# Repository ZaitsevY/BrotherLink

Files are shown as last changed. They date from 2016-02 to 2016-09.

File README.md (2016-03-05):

# Wireless Brother KH-9xx knitting machine connection.

Isn't your Brother KH-9xx online and blogging yet :smile:?<br>
Come on, stop wiring your room, it's time for **IoT** and **WiFi**!<br>
Let's create **wireless** BrotherLink cable!

## TL;DR
[Watch it working](#video)

## Briefly
- Assemble [Hardware](#hardware)
- Upload [Firmware](#firmware)
- Knit with [DesignaKnit](#software-windows-only)

## Introduction

You all know that BrotherLink BLx USB cables are far overpriced. Some of you create 
DIY cables following [Adafruit](https://learn.adafruit.com/electroknit?view=all)
or [Daviworks](http://daviworks.com/knitting/cable_tutorial.html) tutorials.
Having repeated their cable I got an idea to replace the wired connection
with a WiFi one.

After looking around I found that there's a pretty cheap solution out there on
the market – ESP8266 module, which is actually an MCU (micro controller unit)
with built-in SPI flash memory, WiFi, GPIO, UART, etc. periphery. It is very
popular for DIY IoT projects, has a lot of users, who contributed a lot of
libraries helping to develop ESP8266 applications using pure C/C++, Arduino
Wiring, Lua and so on.

## Hardware

I'm not an electronic engineer so I decided to go with ready-to-use modules 
to reduce welding and avoid mistakes. As for the minimum you need:

1. ESP8266 module (or board). I selected [WeMos D1 mini](http://www.wemos.cc/wiki/doku.php?id=en:d1_mini) -
a minimalist ESP8266 board with all necessary resistors, an integrated USB-UART 
bridge (you won't need a separate converter to connect the module to PC for firmware
flashing) and a 5V-to-3.3V power converter (not very reliable though).
2. Logic level converter. Brother KH-9xx serial interface is known to operate at 5V level,
while ESP8266 IO expects 3.3V. The simplest logic level conversion can be achieved with
two resistors by I opted to use a factory manufactured module. I bought mine from
[AliExpress](http://www.aliexpress.com/item/5pcs-lot-4-channel-IIC-I2C-Logic-Level-Converter-Bi-Directional-Module-5V-to-3-3V/32308637756.html)
which is times cheaper than the one from [SparkFun](https://www.sparkfun.com/products/12009).
*Caution*: do not! connect ESP8266 RX/TX directly to KH-9xxx port, doing so will 
most likely harm the module.
3. Power. ESP8266 operates at 3.3V (caution!); to coordinate logic levels you'll
also need 5V. For the time writing the article I feed my device with a breadboard
power supply (note separate +5V and +3.3V buses on the diagram), but for a final
setup I'm going to pick up +5V directly from KH-9xx internals in order to get rid
of wires completely. To step +5V down to +3.3V you should consider including a
separate [AMS1117 power module](http://www.aliexpress.com/item/Free-shipping-5pcs-lot-AMS1117-3-3V-power-supply-module-AMS1117-3-3-power-module-AMS1117/1996263198.html)
(not shown on the diagram). 
4. Optionally, to provide for Interactive Knitting (IK)  mode of the [DesignaKnit](https://www.softbyte.co.uk/designaknit.htm)
application, you might want to add a reed switch and a 10kOm resistor (or, like
did I, use a pre-manufactured [reed switch module](http://www.aliexpress.com/item/Free-Shipping-Reed-sensor-module-magnetron-module-reed-switch-magnetic-switch-for-arduino/1946556259.html)).
You also need a magnet, which you'll put (glue or somehow attach) to the carriage
of the knitting machine (that'll be your BL5 “magnetic arm”). With this option
your device becomes a BrotherLink BL5 wireless cable, while without it – just BL1.

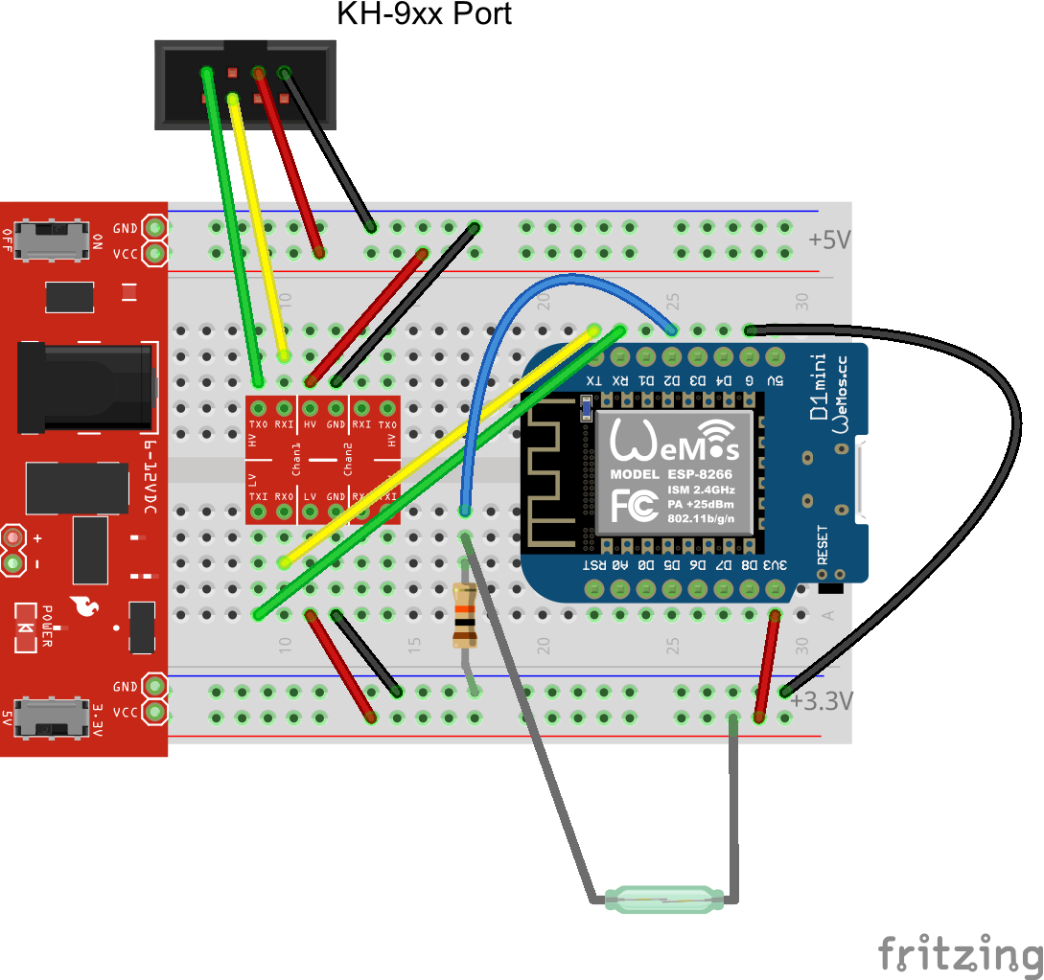
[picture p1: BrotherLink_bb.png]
Diagram


## Firmware

To make things fly you'll have to upload some firmware to the ESP8266.

The best option for those who are not close to MCU firmware programing
is to download ready-to-flash binary files from the [release](../../releases/).

The firmware is based on [esp8266web](https://github.com/pvvx/esp8266web) 
project which already contains almost all the necessary things including: 
WEB Server, TCP-to-UART bridge with a lot of configurable options, device 
and application configuration through web interface.

I had to make some customizations of the original project in order to 
utilize reed switch and provide for Interactive Knitting. Customized 
sources are [here](https://github.com/ZaitsevY/esp8266web/tree/custom) 
and the sources of the application (Eclipse project) are right in this
very repository.
Again, to skip the time consuming learning trail of compiling firmware 
from sources, you might prefer to download the [ready-to-flash binary files](../../releases/).

To upload firmware to your module you'll have to install [Python](https://www.python.org/downloads/) 
(choose 2.x version) with [pyserial](https://pythonhosted.org/pyserial/) 
(the simplest way is to issue `pip install pyserial` from command prompt 
after Python installation). [Esptool](https://github.com/themadinventor/esptool) 
is already included in the binary distribution. If you follow me and use 
WeMos D1 mini module, make sure you have installed [Ch340G driver](http://www.wemos.cc/wiki/doku.php?id=en:ch340g) 
(if appropriate for your OS). 

Connect your module to USB of your PC, detect the resulting COM-port number.<br>
*Note:* COM4 is assumed for the example commands below.<br>
*Note:* click RESET button of D1 mini just before you run `esptool.py … write_flash …` command.

First, flash clear settings with the following from the command prompt:
```
esptool.py --port COM4 --baud 460800 write_flash -ff 80m -fm qio -fs 4m 0x79000 clear_eep.bin 0x7C000 esp_init_data_default.bin 0x7E000 blank.bin
```

Second, flash the software portion:
```
esptool.py --port COM4 --baud 460800 write_flash -ff 80m -fm qio -fs 4m 0x00000 .0x00000.bin 0x07000 .0x07000.bin
```

Press RESET on the module again (just to be on the safe side), wait a
couple of seconds and now you can use any of your WiFi-enabled 
devices (notebook, smartphone) to:

1. Connect to a WiFi access point named ESP8266 (by default);
2. Point you browser to http://192.168.4.1/fsupload (default username:password 
are ESP8266:0123456789) and upload WEBFiles.bin file;
3. Point you browser to http://192.168.4.1/ and continue device configuration.

### Configuration:

1. WiFi Settings: set your home WiFi SSID and password. Optionally switch off 
ESP8266 access point by selecting STATION_MODE. Mention that right after switching 
AP off you won't be able to access web interface of the module with 192.168.4.1, 
instead reconnect your notebook (or whatever) back to your home network and 
use [http://sesp8266/](http://sesp8266/) or, if the latter doesn't work for you,
find out the new module IP address from your WiFi router (notice http://192.168.1.37/ 
address part on the screenshots below). Or just leave WiFi mode setting as STATIONAP_MODE.<br>
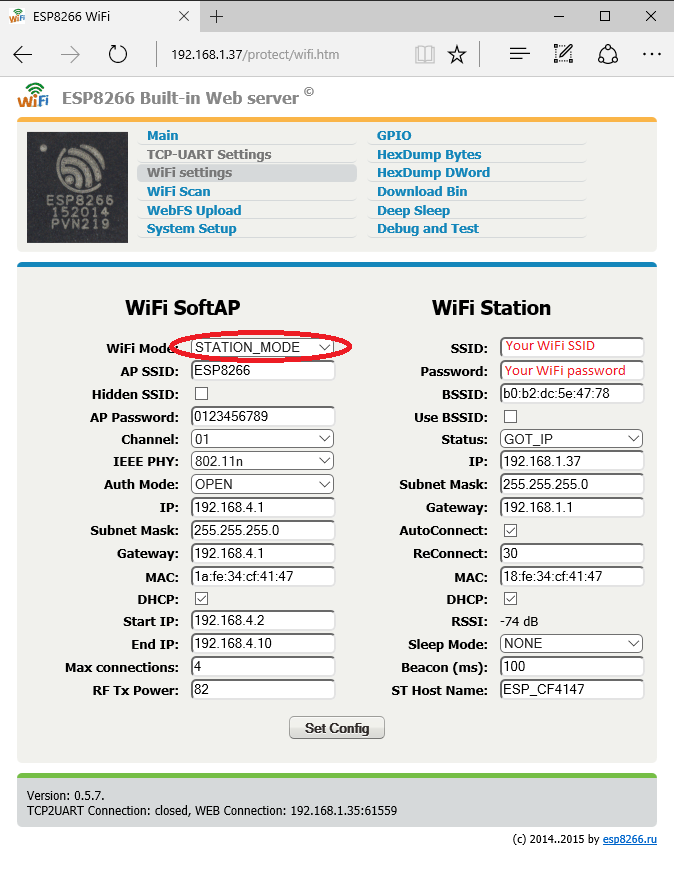
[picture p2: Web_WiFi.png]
WiFi Settings

2. TCP-TO-UART Settings: set baud rate to 9600, enable RX and TX inversion.<br>
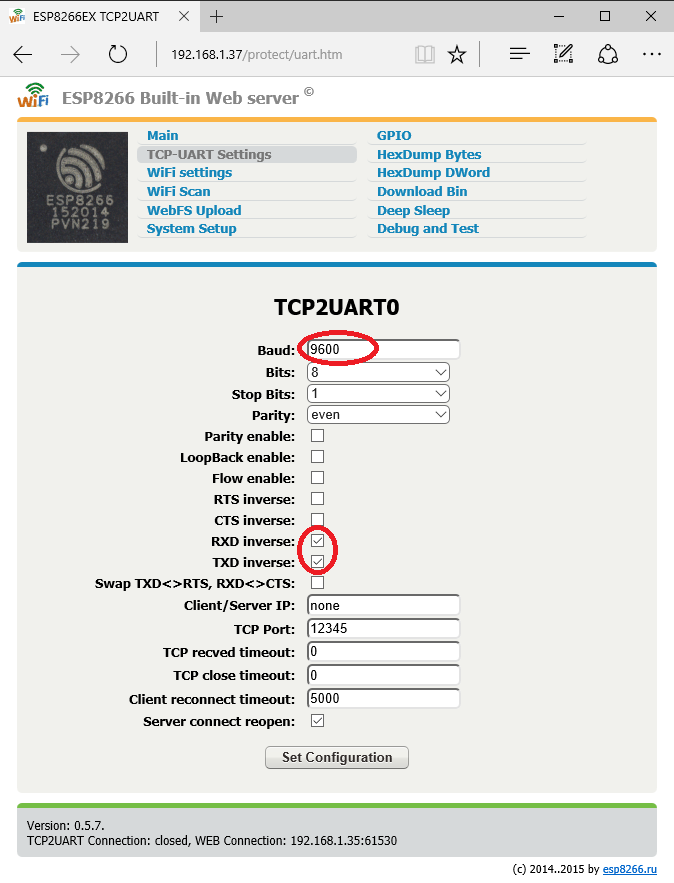
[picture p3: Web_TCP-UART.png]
TCP=UART Settings

3. System Setup: disable checking RX pin to reset WiFi configuration (*important!* 
When you power on your device while it is connected to KH-9xx port, this setting, 
if enabled, will reset your customizations from 1.).<br>
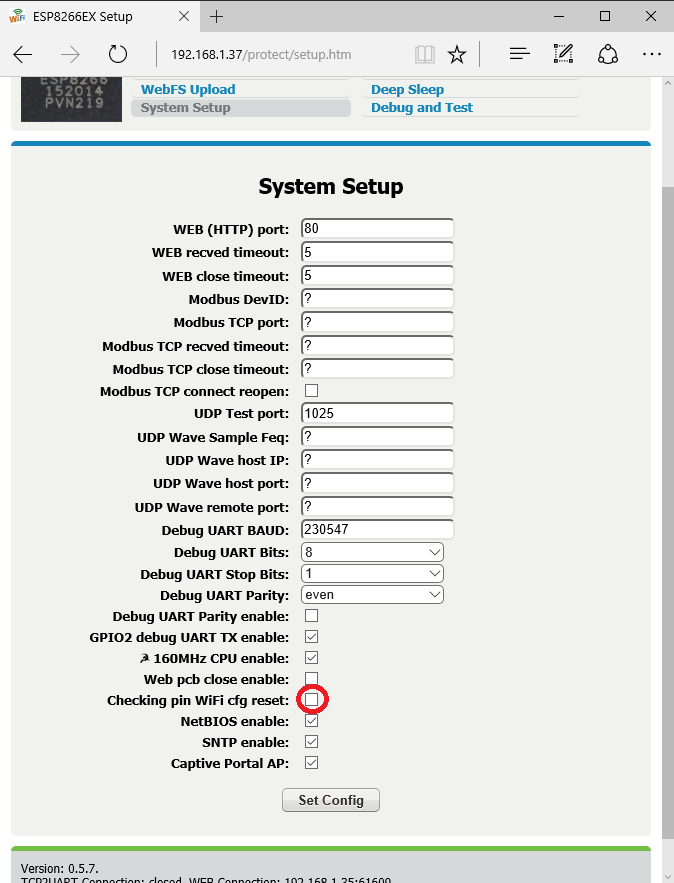
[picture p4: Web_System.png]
System Settings


## Software (Windows only)

DesignaKnit expects knitting machine to be connected through COM interface. 
To make it acquainted with your device you'd install a virtual COM-port driver. 
There are several solutions out there: [HW VSP](http://www.hw-group.com/products/hw_vsp/index_en.html), 
[VSPE](http://www.eterlogic.com/Products.VSPE.html), 
[USR-VCOM](http://www.usriot.com/Download/31.html); 
I didn't try them all so the following screen shots are all about HW VSP.

After installing HW VSP you'd create a virtual COM-port with the following settings:

First, at the Settings tab, click Login to acquire administrative access, 
then configure as on the following screen shot:<br>
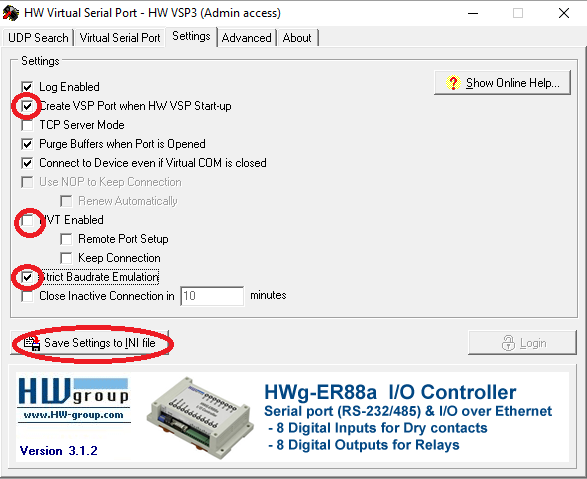
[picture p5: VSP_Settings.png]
VSP Settings


Next, go to the Virtual Serial Port tab to select your COM-port name; set “sesp8266” for 
the IP-address (or take the IP of your device from its web interface WiFi Settings 
page, IP from WiFi Station column); set port to 12345:<br>
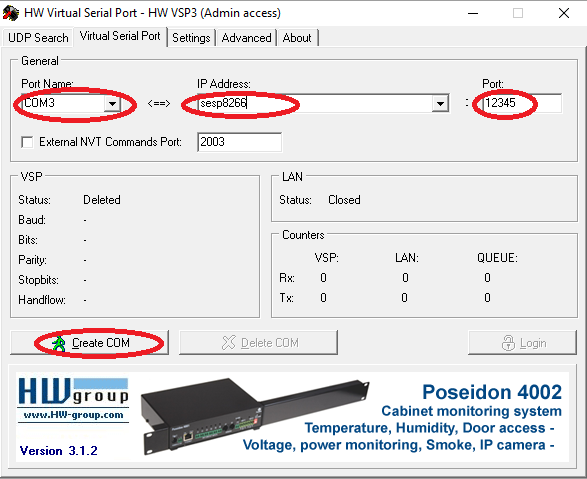
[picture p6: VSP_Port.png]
VSP Virtual Port


*Note:* if you power your device off, HW VSP looses connection to your device
and to enable it again you'll have to delete and create your virtual port again.
Looks like "Use NOP to Keep Connection" and "Renew Automatically" settings of
HW VSP might help but they are by some reason disabled.

## Video

Finally it's time to DesignaKnit!

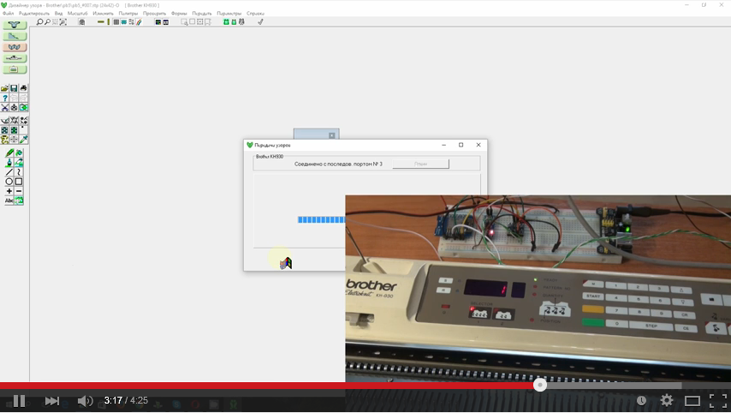
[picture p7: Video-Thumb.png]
Wireless Brother KH-9xx connection (https://youtu.be/KoAtUXrqRgE)


## Acknowlegements

- Great knitting machine interface analysis by Graham Wideman at 
https://grahamwideman.wikispaces.com/Knitting+machine+interfaces
- Splendid ESP8266 project by Victor at https://github.com/pvvx/esp8266web

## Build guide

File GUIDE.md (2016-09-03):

# Wireless BrotherLink

## Package contents

- Wireless BrotherLink device
- Piece of double sided tape
- Magnet

## Power

The device is powered with 5V (USB-plug), you can use any modern smartphone wall charger.
Also any PC/notebook USB-port can be used (though not recommended).

## Knitting machine connection.

The device has a plug for connection to the knitting machine port.
There's a mark (a perforation) on top of the plug for proper orientation.

## WiFi configuration

Power the device on. After initialization (5..10 seconds) a new WiFi Access Point
named "ESP8266" by default is established. Now you can use any WiFi-capable device 
(notebook, tablet, smartphone) to:
- connect to ESP8622 network;
- point you browser to http://192.168.4.1
- revise or change device settings, default login and password are "ESP8266":"0123456789";

You might wish to configure device to connect to your home WiFi (if available).
Visit "WiFi Settings" page and under "WiFi Station" section fill "SSID" and "Password", 
check "AutoConnect" and press "Set Config". After a while (30..60 secods) reload
the page and make sure that "Status" has changed to "GOT_IP" indicating successful
connection of the device to your home WiFi network. Optionally you can now switch
ESP8266 Access Point off by selecting "WiFi Mode" STATION_MODE at "WiFi SoftAP" section.
Or you can leave this setting STATIONAP_MODE. 
After device is connected to your home WiFi, your notebook/smartphone/etc can now 
leave ESP8266 and return to your home WiFi. The address of the device in your
home network becomes "sesp8266" (http://sesp8266). If the latter doesn't work
for you, you'll have to get the device's IP-address from your WiFi router.<br>
WiFi Settings

## DesignaKnit configuration

DesignaKnit expects knitting machine to be connected through COM interface. 
To make it acquainted with your device you'd install a virtual COM-port driver. 
There are several solutions out there: [HW VSP](http://www.hw-group.com/products/hw_vsp/index_en.html), 
[VSPE](http://www.eterlogic.com/Products.VSPE.html), 
[USR-VCOM](http://www.usriot.com/Download/31.html); 
I didn't try them all so the following screen shots are all about HW VSP.

After installing HW VSP you'd create a virtual COM-port with the following settings:

First, at the Settings tab, click Login to acquire administrative access 
(default password is "admin"), then configure as on the following screen shot:<br>
VSP Settings

Next, go to the Virtual Serial Port tab to select your COM-port name (COM3 in the example);
set “sesp8266” for the IP-address (or take the IP of your device from its web interface 
WiFi Settings page, IP from WiFi Station column); set port to 12345:<br>
VSP Virtual Port

It might take 10..30 seconds after you click "Create COM" until VSP creates and mounts the port.
After that it's high time to launch DesignaKnit and use it to download or upload patterns,
just don't forget to set COM-port number in the settings.

*Note:* if you power your device off, HW VSP looses connection to your device
and to enable it again you'll have to delete and create your virtual port again.
Looks like "Use NOP to Keep Connection" and "Renew Automatically" settings of
HW VSP might help but they are by some reason disabled.

## Interactive knitting

Put a magnet from the package contents (or any other one) onto the arm of the 
knitting machine carriage and fix it with scotch tape.
Position the device on top of the machine (you may use the provided piece of double 
sided tape to fix it) so, that the arm with the magnet will pass the reed switch
at a distance of 3..5 mm. There's a led which will flash when the reed switch 
detects the magnet pass. Now you're ready for interactive mode.

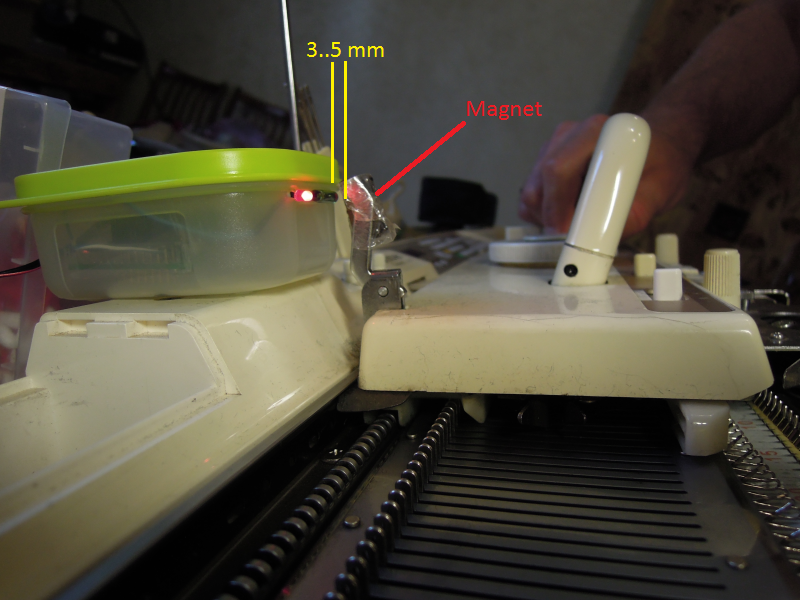
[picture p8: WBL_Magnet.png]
Magnet position


*Note:* when knitting with patterns, the arm with a magnet should not be in
lower position because the magnet can interfere with the knitting machine
build-in sensors.

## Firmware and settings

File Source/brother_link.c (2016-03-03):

#include "user_config.h"
#ifdef USE_TCP2UART
#include "c_types.h"
#include "os_type.h"
#include "tcp2uart.h"
#include "user_interface.h"
#include "bios/gpio.h"
#include "hw/esp8266.h"
#include "phy/phy.h"
#include "web_iohw.h"

//===============================================================================
// Application: Data -> TCP
// Передать данные текущему TCP соединению.
// Позволяет программно дополнить поток данных от UART.
// Внимание: в текущей реализации отсылка идет в обход
// буфера UART напрямую в LwIP стэк, т.е. нарушает
// целостность потока данных от UART (которая, собственно,
// и так нарушена наличием этого вызова).
// Нельзя! вызывать из обработчиков прерываний напрямую.
//-------------------------------------------------------------------------------
err_t tcp2uart_write(uint8 *pblk, uint16 len)
{
	uint8* buffer = uart_drv.uart_rx_buf;
	if (buffer == NULL) return ERR_CONN;

	// Going to touch buffers usually filled by UART
	// interrupt handler: disable interrupts temporary.
	ETS_INTR_LOCK();

	// Number of bytes in buffer so far
	uint32 length = uart_drv.uart_rx_buf_count;
	if (length >= UART_RX_BUF_MAX
			|| uart_drv.uart_nsnd_buf_count >= UART_RX_BUF_MAX
			|| len > UART_RX_BUF_MAX - length) {
		// No space in buffer
		ETS_INTR_UNLOCK();
		return ERR_INPROGRESS;
	}

	// Copy data into buffer
	while (length < UART_RX_BUF_MAX && len--)
		uart_drv.uart_rx_buf[length++] = *pblk++;
	uart_drv.uart_rx_buf_count = length;

	// Number of non-delivered bytes
	length -= uart_drv.uart_out_buf_count;
	if (length) {
		// Request TCP2UART to deliver to TCP peer
		system_os_post(UART_TASK_PRIO, UART_RX_CHARS, length);
		uart_drv.uart_nsnd_buf_count += length;
		uart_drv.uart_out_buf_count = uart_drv.uart_rx_buf_count;
	}

	// Finished
	ETS_INTR_UNLOCK();
	return ERR_OK;
}

#define BUTTON_GPIO 4	// GPIO4
#define BUTTON_TASK_PRIO (USER_TASK_PRIO_1)
#define BUTTON_TASK_QUEUE_LEN 2
static const uint32 BUTTON_CLICK_DELAY = 400*1000;	// Next click not earlier than after, ms
static const GPIO_INT_TYPE BUTTON_INTR = GPIO_PIN_INTR_NEGEDGE;

os_event_t _queue[BUTTON_TASK_QUEUE_LEN] DATA_IRAM_ATTR;
uint32 _click DATA_IRAM_ATTR = 0;
uint32 _count DATA_IRAM_ATTR = 0;

/**
 * GPIO interrupt handler.
 */
static void intr_brother_link(void) {
	// Read GPIO status
	uint32 gpio_status = GPIO_STATUS;
	// Acknowledge GPIO interrupt
	GPIO_STATUS_W1TC = gpio_status;
	// Is is from mine reed switch?
	if (gpio_status & (1 << BUTTON_GPIO)) {
		// Schedule task execution
		system_os_post(BUTTON_TASK_PRIO, 0, 0);
		// Call me again next time
	    gpio_pin_intr_state_set(BUTTON_GPIO, BUTTON_INTR);
	}
}

/**
 * Reed switch task handler.
 * Send "click" to DesignaKnit.
 */
static void ICACHE_FLASH_ATTR task_brother_link(os_event_t *e)
{
	uint32 clock = system_get_time();
	if (clock < _click) {
		// System time overflow
		_click = 0;
	}
	if (e->par || clock >= _click + BUTTON_CLICK_DELAY) {	// Forced? or time to click?
		uint8 letter = (_count % 10) + '0';		// Actually just any symbol works
		if (ERR_INPROGRESS == tcp2uart_write(&letter, sizeof(letter))) {
			// Could not send, retry again later (forced)
			system_os_post(BUTTON_TASK_PRIO, 0, 1);
		} else {
			// Fine, just remember that shiny moment
			_click = clock;
			_count++;
		}
	}
}

/**
 * BrotherLink initialization.
 */
void ICACHE_FLASH_ATTR init_brother_link(void)
{
 	os_printf("\nBrotherLink...\n");

 	// Store initialization time
	_click = system_get_time();

	// Register event queue
	system_os_task(task_brother_link, BUTTON_TASK_PRIO, _queue, BUTTON_TASK_QUEUE_LEN);

	// Configure GPIO for reed switch
	uint32 pins_mask = (1 << BUTTON_GPIO);
	ETS_GPIO_INTR_DISABLE();
	gpio_output_set(0, 0, 0, pins_mask);	// configure pin for input
	set_gpiox_mux_func_ioport(BUTTON_GPIO);	// set pin function to GPIO
	ETS_GPIO_INTR_ATTACH(intr_brother_link, NULL);	// attach interrupt handler
	gpio_pin_intr_state_set(BUTTON_GPIO, BUTTON_INTR);	// to fire on condition
	GPIO_STATUS_W1TC = pins_mask;			// clear any GPIO interrupts
	ETS_GPIO_INTR_ENABLE();
}

/**
 * Custom initialization sequence implementation.
 */
void ICACHE_FLASH_ATTR custom_init() {
	init_brother_link();
}

#endif

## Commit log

2016-02-24 Source code and readme with screenshots
    [BrotherLink.fzz]
2016-03-02 HW VSP: enabling "Strict Baudrate Emulation" is important to avoid device's memory overflow (causes fatal exception and reboots)
